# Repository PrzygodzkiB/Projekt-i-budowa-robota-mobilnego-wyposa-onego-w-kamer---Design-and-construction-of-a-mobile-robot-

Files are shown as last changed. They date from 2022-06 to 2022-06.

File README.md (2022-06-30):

# Design and construction of a mobile robot 
## English
This engineering thesis is written in Polish. However, if someone wants to see the code for ESP 32 CAM microcontrollers for transmitting the image from the camera and ESP 32 for controlling the control via wifi, you are welcome. 

The work presents the construction process and implementation of a mobile robot software
equipped with a camera. Its assumption is to construct a remotely controlled unit enabling
smooth image transmission. The scope of work is also related to the commissioning and testing
of the constructed structure.

The completed vehicle was designed to work well at home. It was with this in mind that
the engines and the platform were selected. During the design stage, it was decided to use
two microcontrollers, due to the limitations of one of them and the desire to liquefy the
camera image. The method of selecting a driver for motors, sonars, power source and voltage
stabilizer has also been described. When designing the electronic part, care was taken to ensure
the appropriate temperature of the system and safety in the event of short circuits. Schematic
diagrams and block diagrams of electrical connections in the system are also presented. There
is also a description of two hand-designed PCBs.

As part of the work, the robot successfully communicated with the user via wi-fi. A website
was also written to serve as a driving control panel. It contains the image from the robot’s
camera as well as the results of distance and voltage measurements. UART’s communications
were also used to pass commands between the microcontrollers.

In order to drive the robot in a straight line, three methods of regulation were compared.
They were made on the basis of PI regulators, which synchronized the work of the engines or
did not do it. There are also written anti-collision functions while driving based on distance
measurements made with the use of sonars.
## Polish

Praca przedstawia proces budowy oraz implementację oprogramowania robota mobilnego
wyposażonego w kamerę. Jej założeniem jest skonstruowanie zdalnie sterowanej jednostki
umożliwiającej płynne przekazywanie obrazu. Zakres pracy wiąże się również z uruchomieniem
i przetestowaniem wykonanej konstrukcji.

Analizując tematykę zagadnienia, dokonano zestawienia trzech robotów z kamerą. Do
tego celu wybrano konstrukcje o zróżnicowanej budowie oraz przeznaczeniu. Z ich opisów
zaczerpnięto zastosowania później wykorzystane we własnym robocie.

Wykonany pojazd został zaprojektowany tak, aby sprawdzał się w warunkach domowych.
Pod tym kątem dokonano wyboru silników oraz platformy. W czasie projektowania zdecydowano
się na użycie dwóch mikrokontrolerów, z powodów ograniczeń jednego z nich oraz
z chęci upłynnienia obrazu kamery. Dokonano również opisu sposobu doboru sterownika
silników, sonarów, źródła zasilania oraz stabilizatora napięcia. Projektując część elektroniczną,
zadbano o odpowiednią temperaturę układu oraz o bezpieczeństwo w przypadku wystąpienia
zwarć. Przedstawiono też schematy ideowe oraz blokowe połączeń elektrycznych w układzie.
Umieszczono również opis dwóch własnoręcznie zaprojektowanych płytek PCB.

W ramach pracy dokonano udanej komunikacji robota z użytkownikiem za pomocą wi-fi.
Napisano również stronę internetową służącą jako panel kontroli jazdy. Witryna wyświetla obraz
z kamery robota oraz wyniki pomiarów odległości i napięcia. Zastosowano również komunikacje
UART w celu przekazywania poleceń między mikrokontrolerami.

Aby zrealizować jazdę robota po linii prostej, dokonano porównania trzech sposobów
regulacji. Były one zrealizowane na postawie regulatorów PI, które synchronizowały prace
silników lub tego nie robiły. Napisano również funkcje zabezpieczające przed kolizją w czasie
jazdy na podstawie pomiarów odległości wykonywanych za pomocą sonarów.

W czasie testów dokonano oceny otrzymywanego obrazu. Okazał on się płynny i wyraźny
na tyle, by zidentyfikować co, znajduje się w otoczeniu robota. Za pomocą wyników testu
jazdy po linii prostej wykonano zestawienie osiągnięć różnych sposobów sterowania. Udało
się dzięki temu wytypować najlepszy z nich. Dokonano również sprawdzenia bezkolizyjności
robota. Zastosowane sonary okazały się wystarczające, jednak znaleziono też wady użytego
zastosowania. Można uznać, że całościowy projekt sprawdził się w swoim przeznaczeniu.

## Pictures

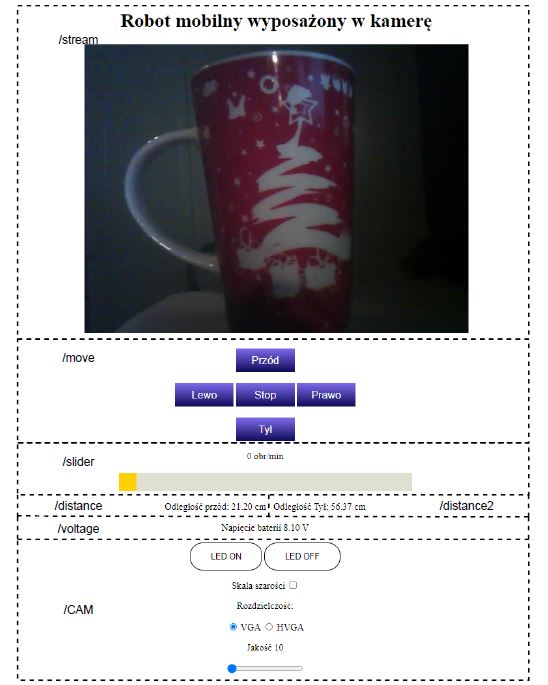
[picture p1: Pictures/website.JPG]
website to communicate with robot


Website to communicate with robot

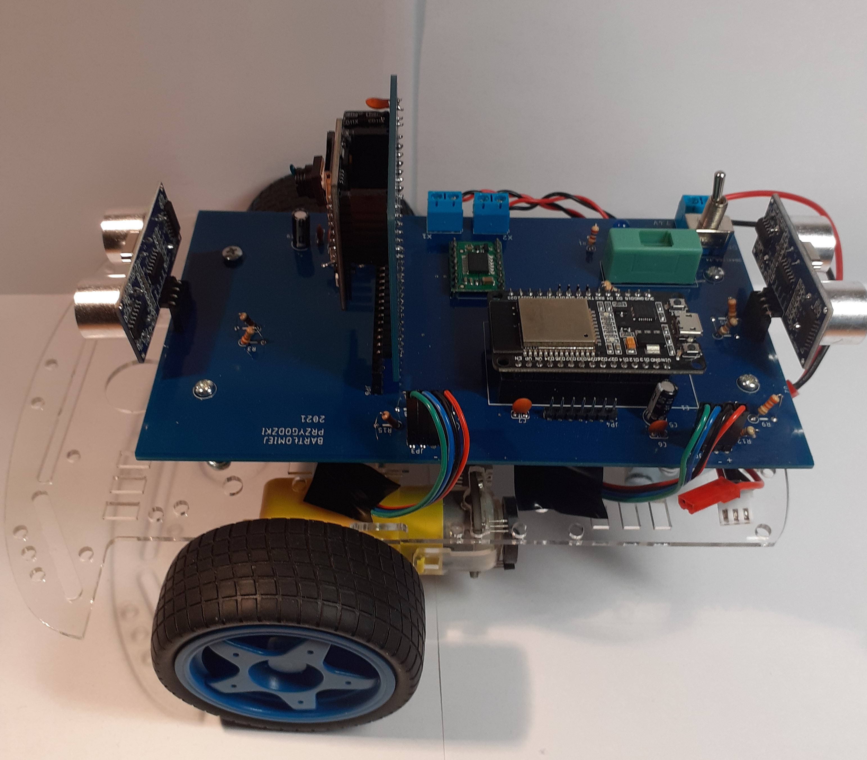
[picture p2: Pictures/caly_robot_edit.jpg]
Robot


Robot

Feel free to use

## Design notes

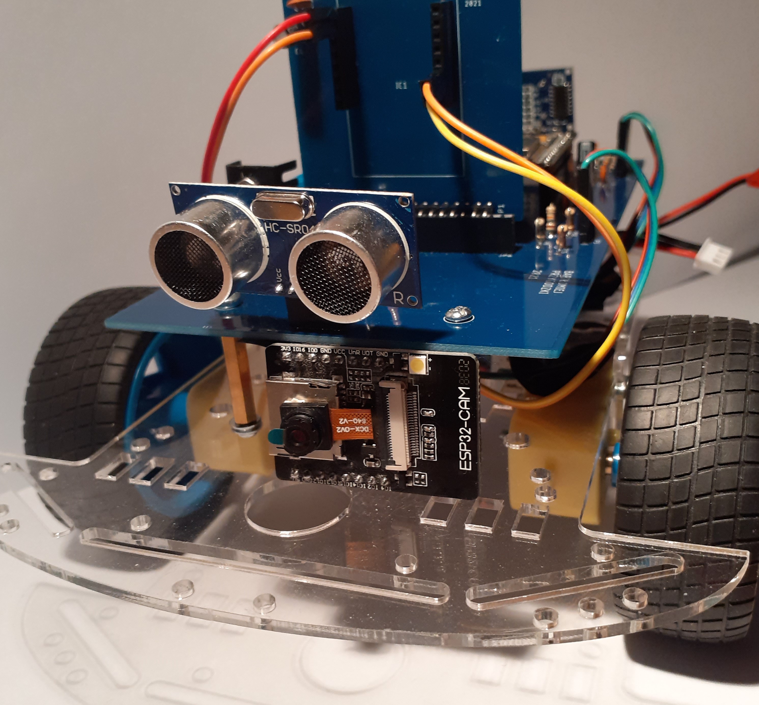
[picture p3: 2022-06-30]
Pictures/robot_inne_ustawienie_kamery.jpg

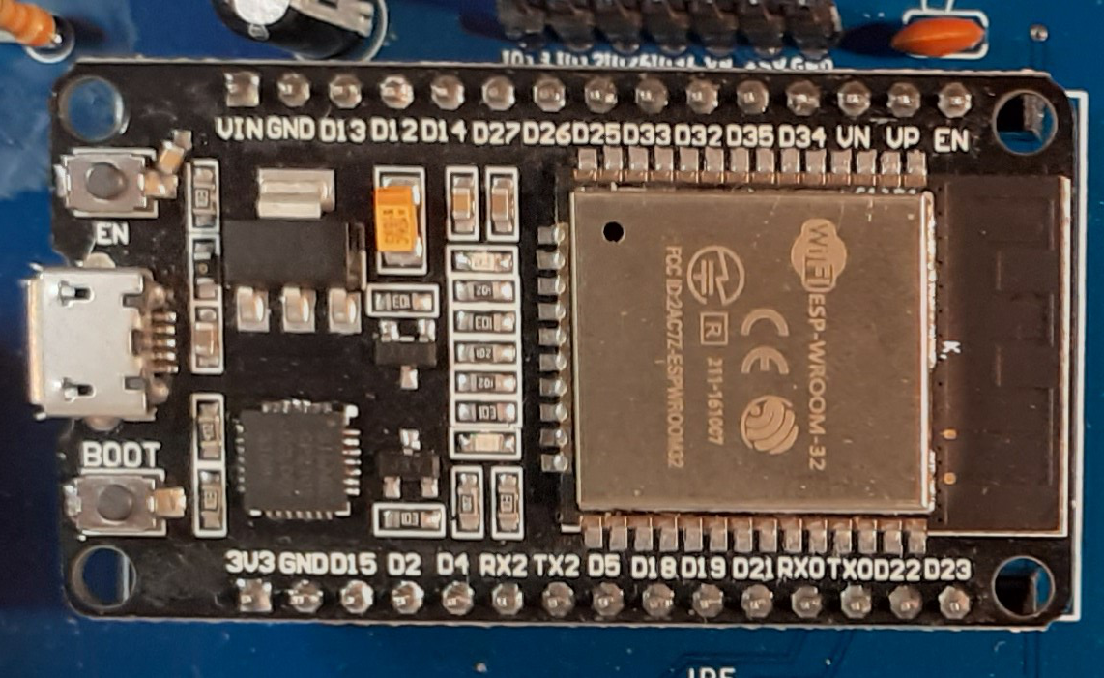
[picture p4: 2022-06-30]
Pictures/devkit.jpg

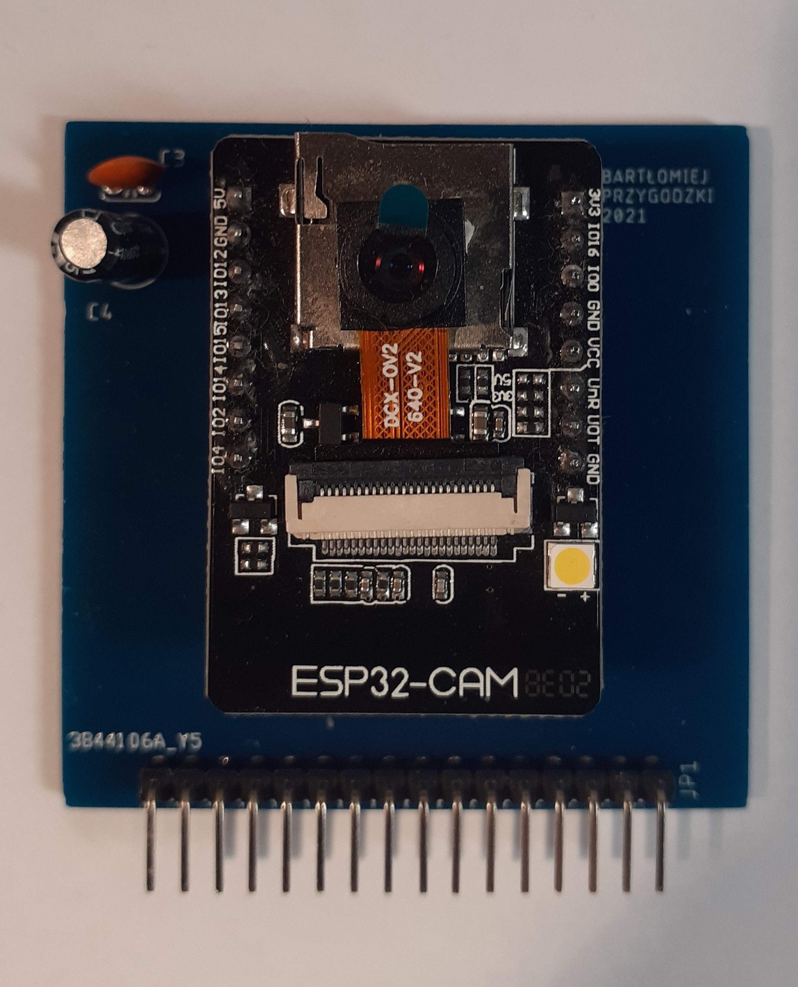
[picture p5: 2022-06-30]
Pictures/Płytka_z_ESP32CAM_edit.jpg

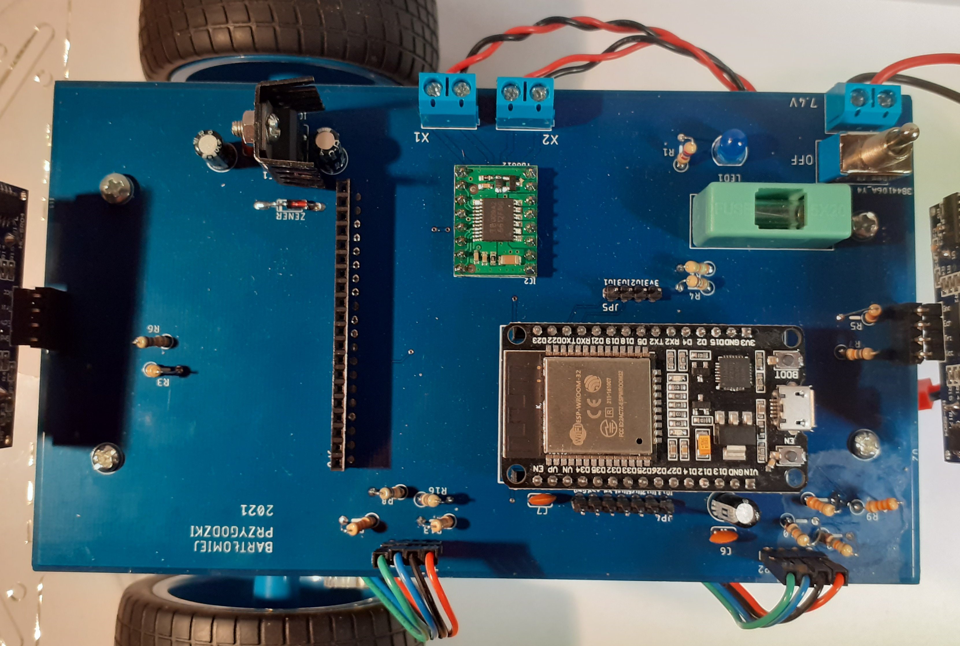
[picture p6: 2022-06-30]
Pictures/płytka_główna_edit.jpg

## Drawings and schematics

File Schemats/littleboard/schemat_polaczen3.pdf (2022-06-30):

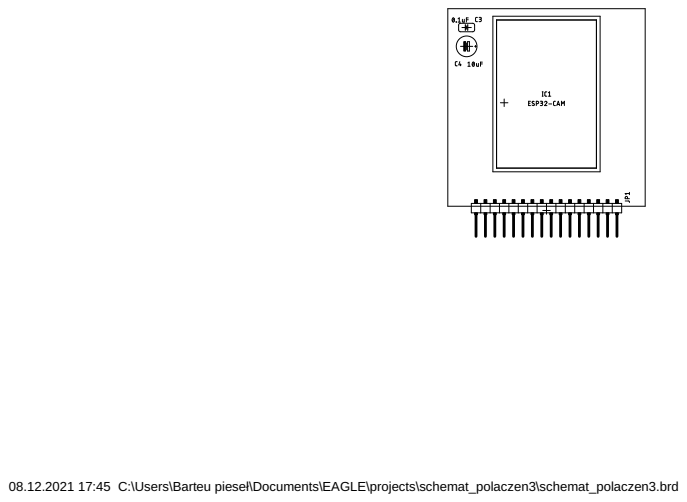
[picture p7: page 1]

08.12.2021 17:45 C:\Users\Barteu pieseł\Documents\EAGLE\projects\schemat_polaczen3\schemat_polaczen3.brd

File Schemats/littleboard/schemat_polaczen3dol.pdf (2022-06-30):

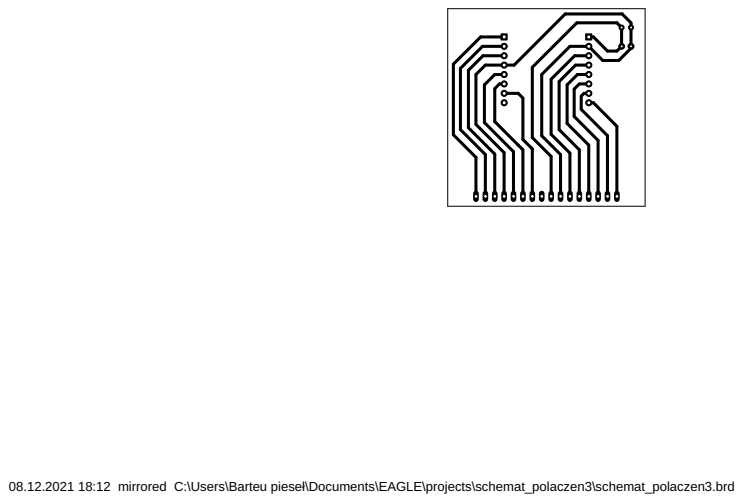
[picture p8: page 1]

08.12.2021 18:12 mirrored C:\Users\Barteu pieseł\Documents\EAGLE\projects\schemat_polaczen3\schemat_polaczen3.brd

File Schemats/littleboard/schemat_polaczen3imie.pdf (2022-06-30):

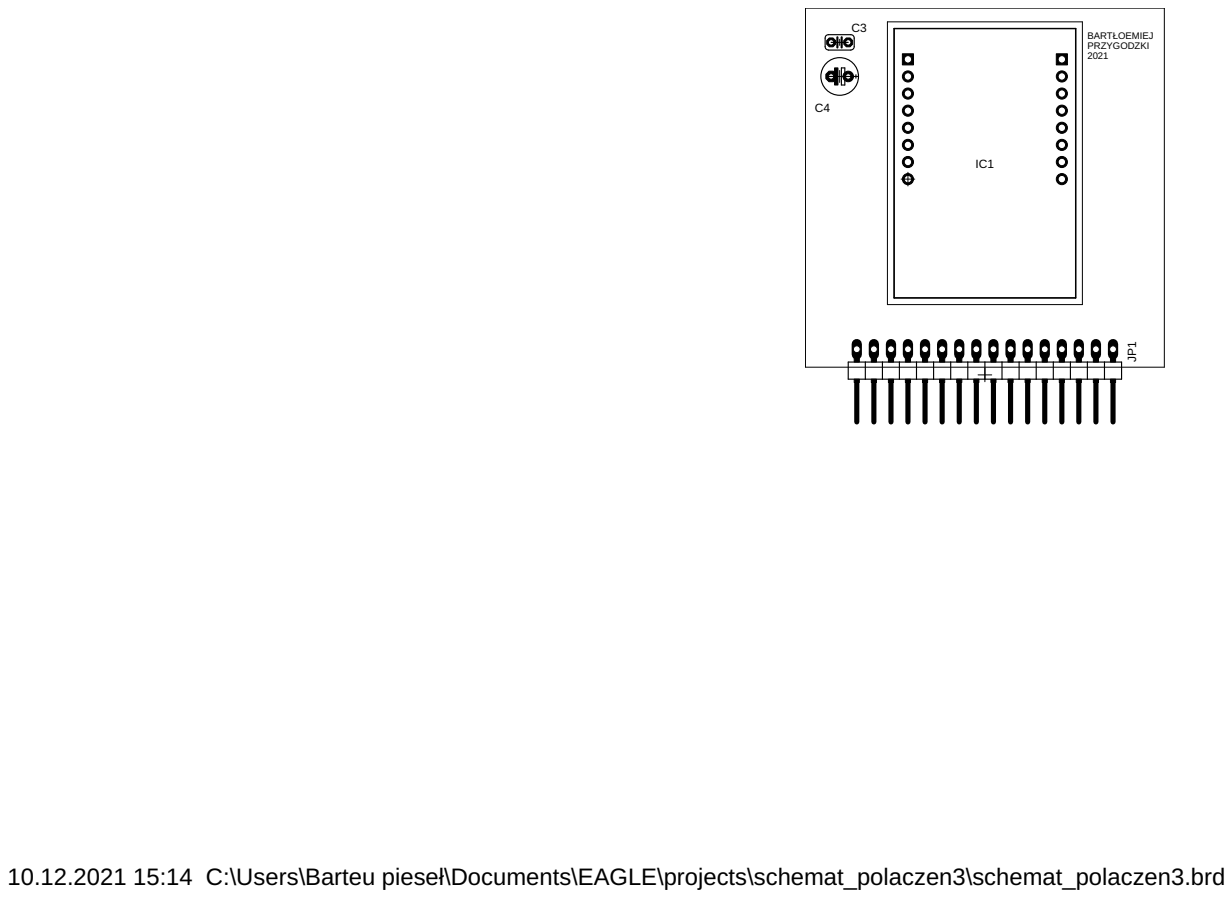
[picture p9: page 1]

10.12.2021 15:14 C:\Users\Barteu pieseł\Documents\EAGLE\projects\schemat_polaczen3\schemat_polaczen3.brd

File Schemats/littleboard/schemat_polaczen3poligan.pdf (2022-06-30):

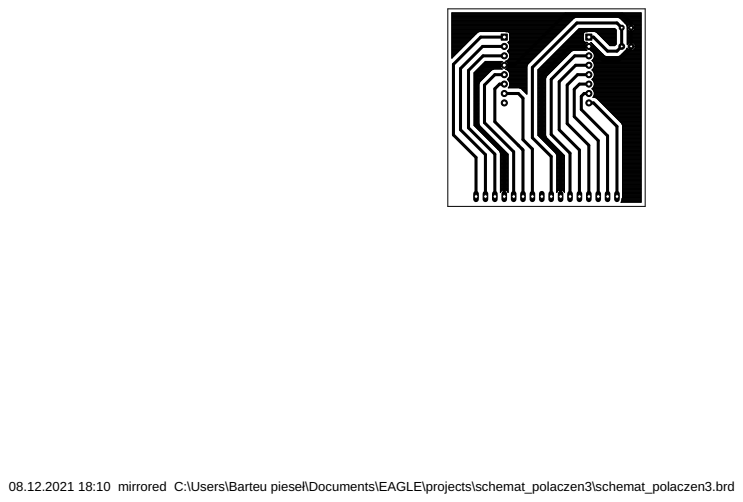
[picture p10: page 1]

08.12.2021 18:10 mirrored C:\Users\Barteu pieseł\Documents\EAGLE\projects\schemat_polaczen3\schemat_polaczen3.brd

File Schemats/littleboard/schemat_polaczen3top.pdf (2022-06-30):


08.12.2021 17:45 C:\Users\Barteu pieseł\Documents\EAGLE\projects\schemat_polaczen3\schemat_polaczen3.brd

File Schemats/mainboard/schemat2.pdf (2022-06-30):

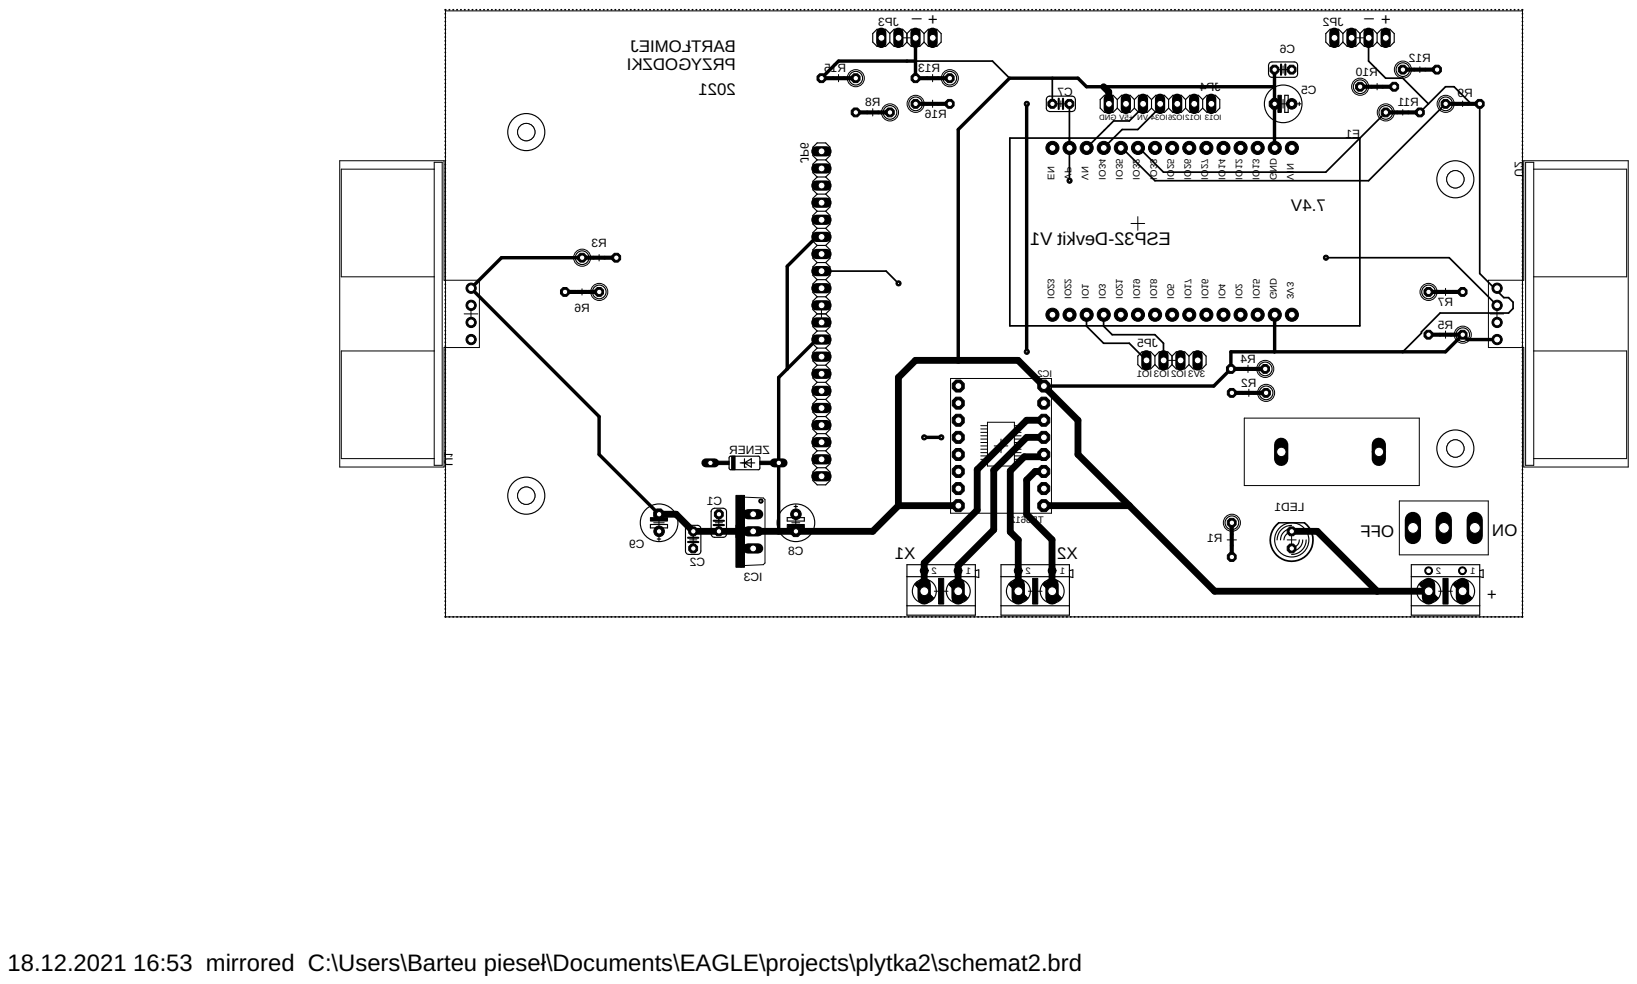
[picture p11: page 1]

18.12.2021 16:53 mirrored C:\Users\Barteu pieseł\Documents\EAGLE\projects\plytka2\schemat2.brd

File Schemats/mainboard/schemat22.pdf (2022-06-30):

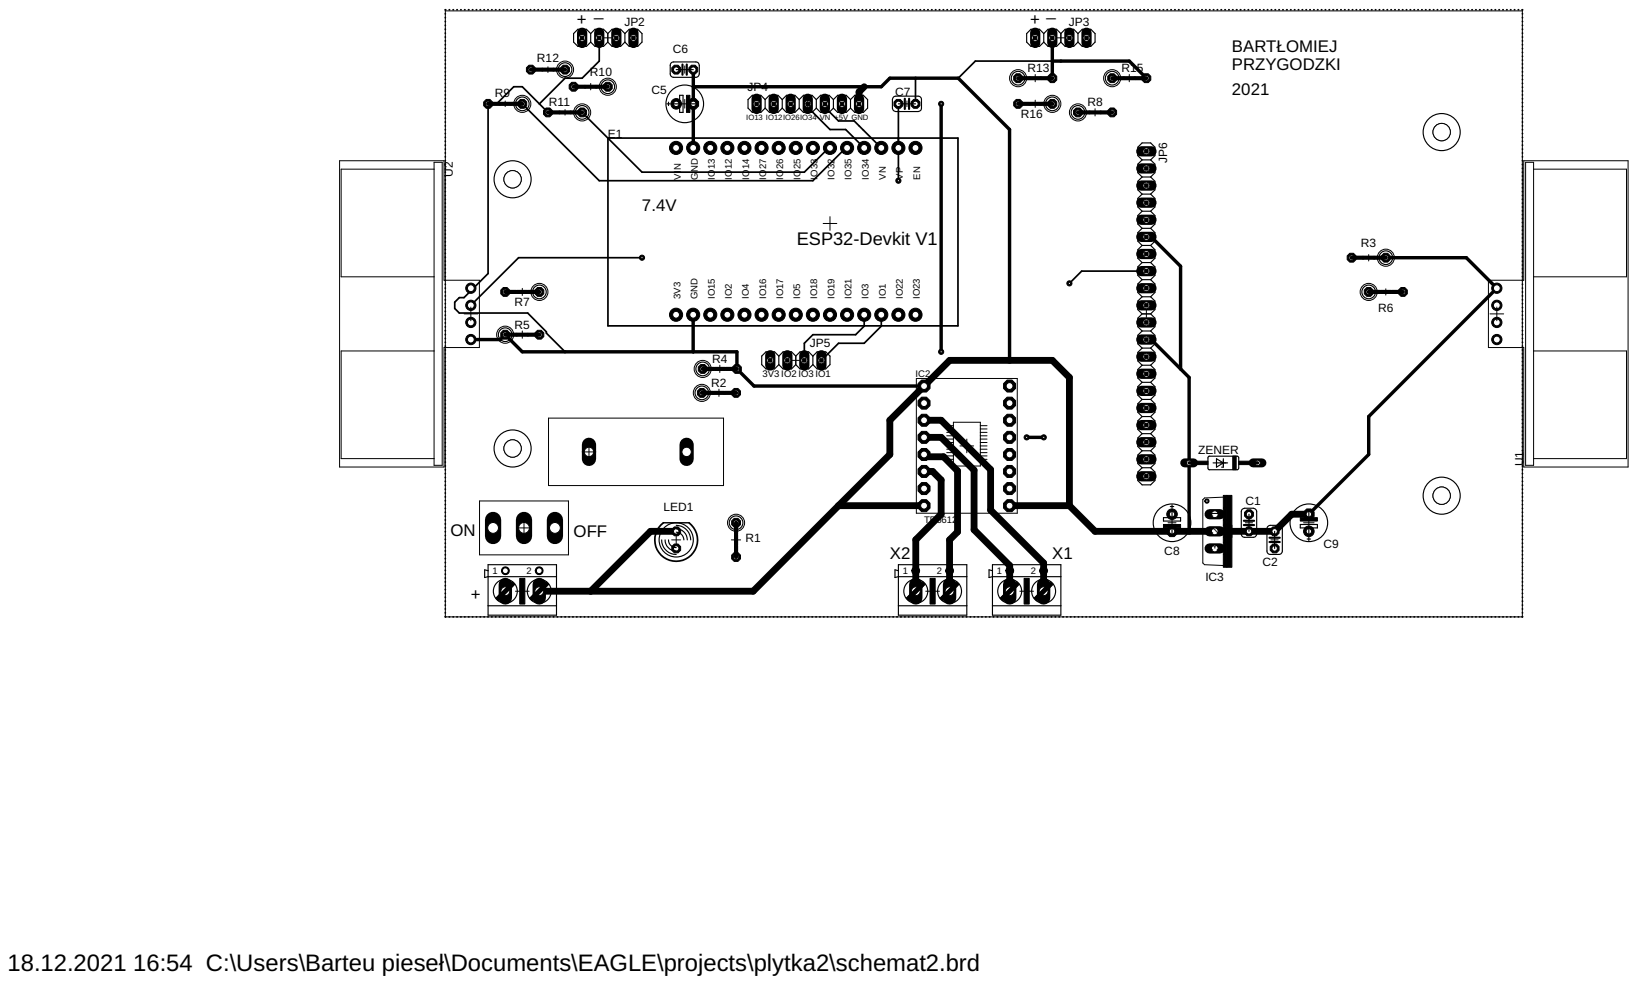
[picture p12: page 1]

18.12.2021 16:54 C:\Users\Barteu pieseł\Documents\EAGLE\projects\plytka2\schemat2.brd

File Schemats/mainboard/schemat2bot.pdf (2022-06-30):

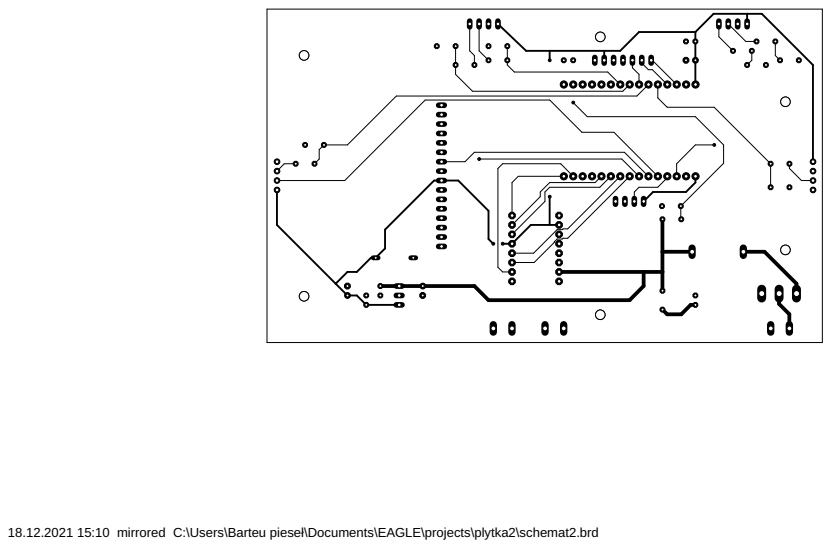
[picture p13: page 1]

18.12.2021 15:10 mirrored C:\Users\Barteu pieseł\Documents\EAGLE\projects\plytka2\schemat2.brd

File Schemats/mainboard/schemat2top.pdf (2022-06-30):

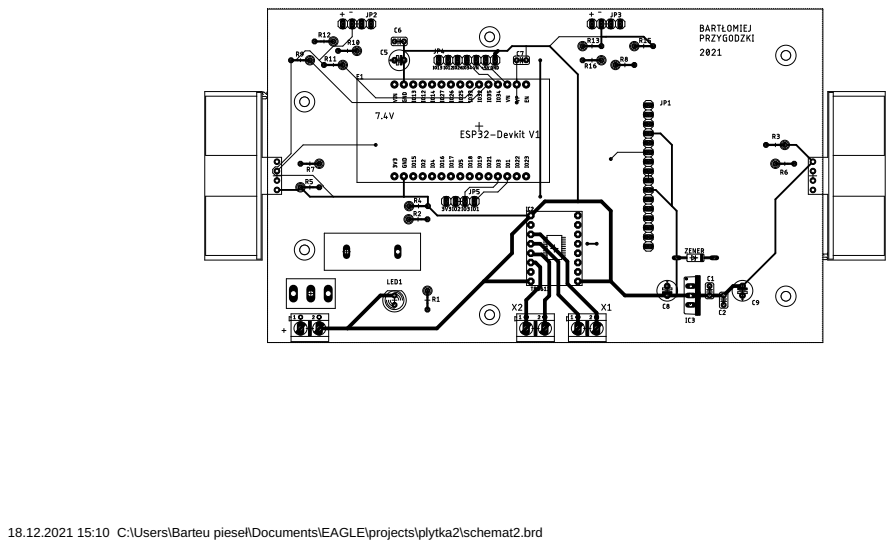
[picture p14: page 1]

18.12.2021 15:10 C:\Users\Barteu pieseł\Documents\EAGLE\projects\plytka2\schemat2.brd

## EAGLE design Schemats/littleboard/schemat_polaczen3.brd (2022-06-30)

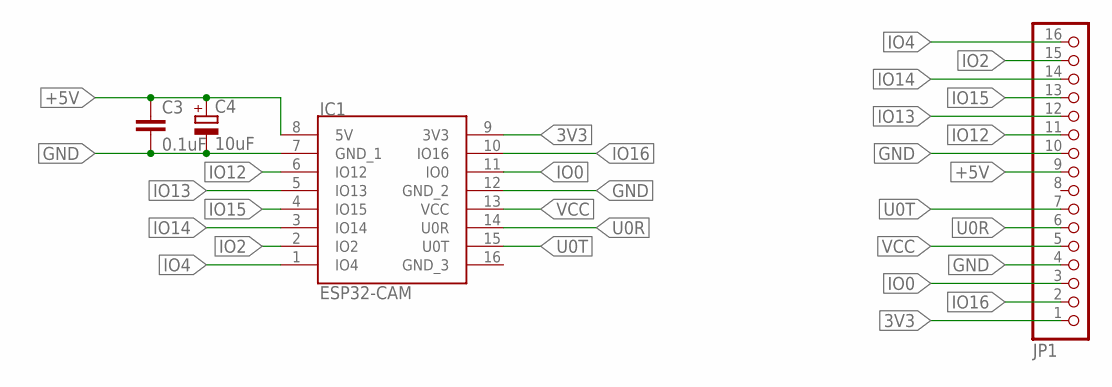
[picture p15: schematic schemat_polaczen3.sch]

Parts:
C3: 0.1uF; C025-024X044
C4: 10uF; E2,5-6E
IC1: ESP32-CAM; ESP32CAM
JP1: PINHD-1X16/90; 1X16/90

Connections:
3V3: IC1.9 (3V3), JP1.1
+5V: C3.1, C4.+, IC1.8 (5V), JP1.9
GND: C3.2, C4.-, IC1.7 (GND_1), IC1.12 (GND_2), JP1.4, JP1.10
IO0: IC1.11 (IO0), JP1.3
IO2: IC1.2 (IO2), JP1.15
IO4: IC1.1 (IO4), JP1.16
IO12: IC1.6 (IO12), JP1.11
IO13: IC1.5 (IO13), JP1.12
IO14: IC1.3 (IO14), JP1.14
IO15: IC1.4 (IO15), JP1.13
IO16: IC1.10 (IO16), JP1.2
U0R: IC1.14 (U0R), JP1.6
U0T: IC1.15 (U0T), JP1.7
VCC: IC1.13 (VCC), JP1.5

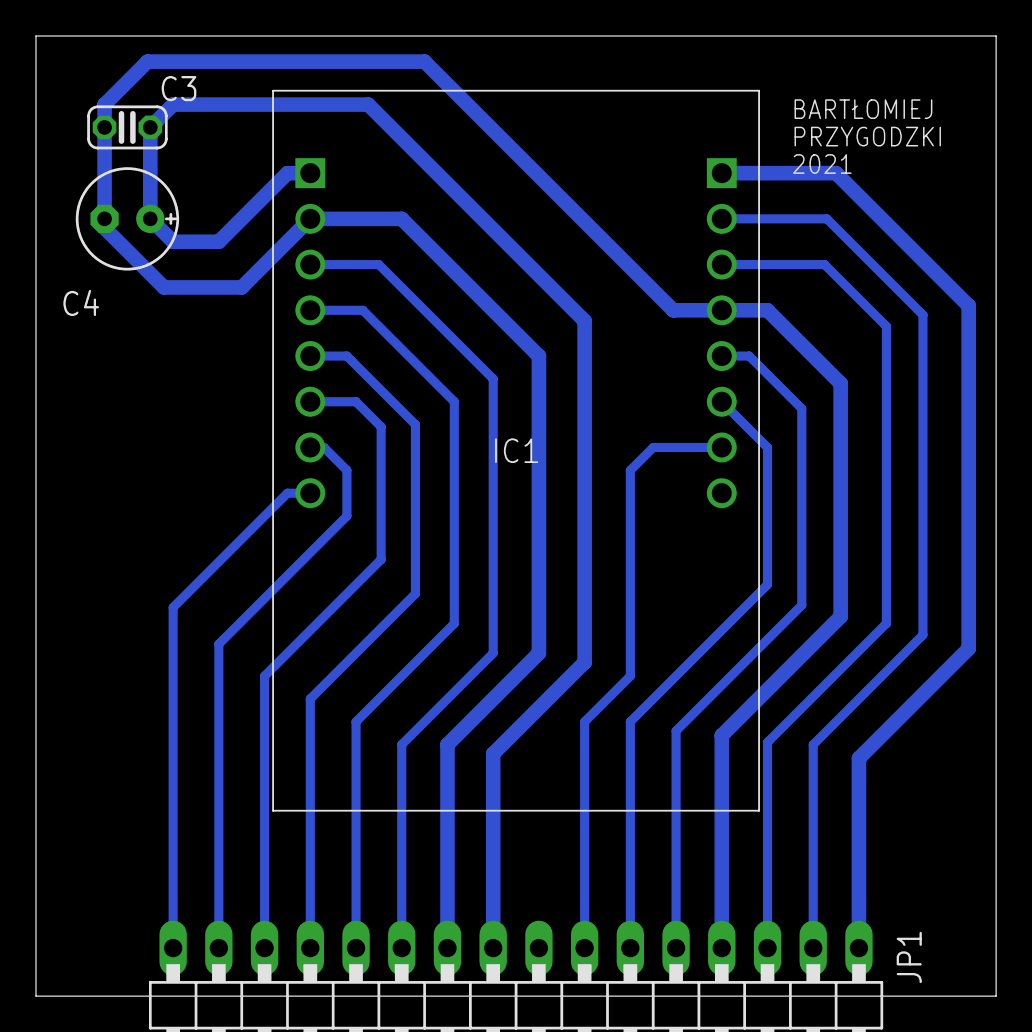
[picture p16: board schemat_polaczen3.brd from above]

Board: 2 copper layers, 53.3 x 53.3 mm, 4 parts (0 on the bottom side), 14 nets.

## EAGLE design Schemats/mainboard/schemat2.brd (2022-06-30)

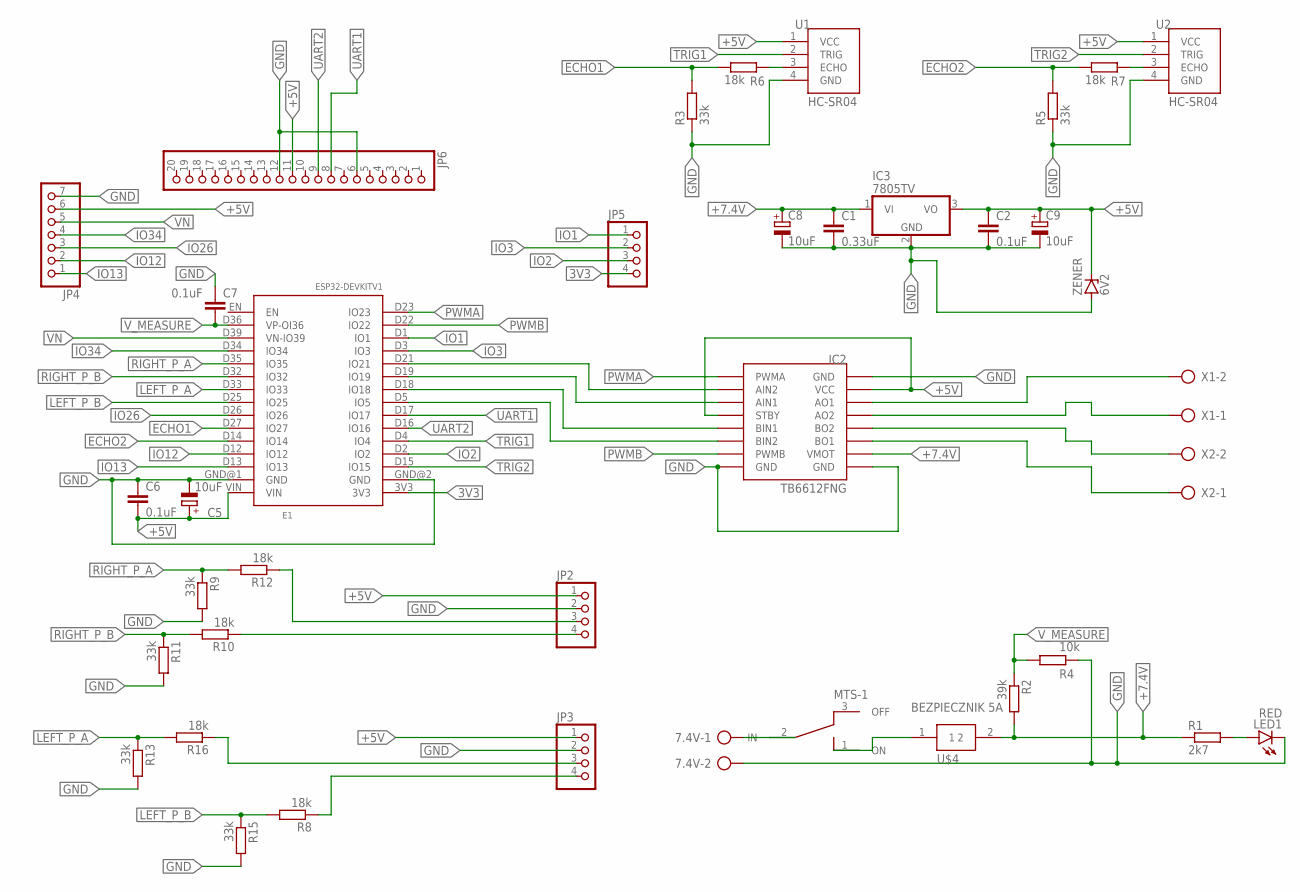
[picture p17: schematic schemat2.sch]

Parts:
7.4V: AK500/2
C1: 0.33uF; C025-024X044
C2, C6, C7: 0.1uF; C025-024X044
C5, C8, C9: 10uF; E2,5-6E
E1: ESP32DEVKITV1; ESP32-DEVKITV1
IC2: MODUL_POLOLU
IC3: 7805TV; TO220V
JP2, JP3, JP5: PINHD-1X4; 1X04
JP4: PINHD-1X7; 1X07
JP6: PINHD-1X20; 1X20
LED1: RED; LED5MM
R1: 2k7; 0207/5V
R2: 39k; 0207/5V
R3, R5, R9, R11, R13, R15: 33k; 0207/5V
R4: 10k; 0207/5V
R6, R7, R8, R10, R12, R16: 18k; 0207/5V
U1, U2: HC-SR04; XCVR_HC-SR04
U$1: MTS-1; SWITCH_TOGGLE
U$4: BEZPIECZNIK 5A; BEZPIECZNIK_GNIAZDO
X1, X2: AK500/2
ZENER: 6V2; DO35Z10

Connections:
3V3: E1.3V3, JP5.4
+5V: C2.1, C5.+, C6.2, C9.+, E1.VIN, IC2.STBY, IC2.VCC, IC3.3 (VO), JP2.1, JP3.1, JP4.6, JP6.11, U1.1 (VCC), U2.1 (VCC), ZENER.C
+7.4V: C1.1, C8.+, IC2.VMOT, IC3.1 (VI), R1.1, R2.2, U$4.2
A: JP3.3, R16.1
A1: JP2.3, R12.1
B: JP3.4, R8.1
B1: JP2.4, R10.1
ECHO1: E1.D27 (IO27), R3.2, R6.1
ECHO2: E1.D14 (IO14), R5.2, R7.1
GND: 7.4V.2, C1.2, C2.2, C5.-, C6.1, C7.1, C8.-, C9.-, E1.GND@1 (GND), E1.GND@2 (GND), IC2.GND1 (GND), IC2.GND2 (GND), IC2.GND3 (GND), IC3.2 (GND), JP2.2, JP3.2, JP4.7, JP6.6, JP6.12, LED1.K (C), R3.1, R4.2, R5.1, R9.2, R11.2, R13.2, R15.2, U1.4 (GND), U2.4 (GND), ZENER.A
IO1: E1.D1 (IO1), JP5.1
IO2: E1.D2 (IO2), JP5.3
IO3: E1.D3 (IO3), JP5.2
IO12: E1.D12 (IO12), JP4.2
IO13: E1.D13 (IO13), JP4.1
IO26: E1.D26 (IO26), JP4.3
IO34: E1.D34 (IO34), JP4.4
LEFT_P_A: E1.D33 (IO33), R13.1, R16.2
LEFT_P_B: E1.D25 (IO25), R8.2, R15.1
L_MOT+: IC2.BO2, X2.2
L_MOT-: IC2.BO1, X2.1
unnamed: LED1.A, R1.2
unnamed: R6.2, U1.3 (ECHO)
unnamed: R7.2, U2.3 (ECHO)
unnamed: 7.4V.1, U$1.2 (IN)
unnamed: E1.D5 (IO5), IC2.BIN2
unnamed: E1.D18 (IO18), IC2.BIN1
unnamed: E1.D21 (IO21), IC2.AIN2
unnamed: E1.D19 (IO19), IC2.AIN1
unnamed: U$1.1 (ON), U$4.1
PWMA: E1.D23 (IO23), IC2.PWMA
PWMB: E1.D22 (IO22), IC2.PWMB
RIGHT_P_A: E1.D35 (IO35), R9.1, R12.2
RIGHT_P_B: E1.D32 (IO32), R10.2, R11.1
R_MOT+: IC2.AO1, X1.2
R_MOT-: IC2.A02 (AO2), X1.1
TRIG1: E1.D4 (IO4), U1.2 (TRIG)
TRIG2: E1.D15 (IO15), U2.2 (TRIG)
UART1: E1.D17 (IO17), JP6.8
UART2: E1.D16 (IO16), JP6.9
VN: E1.D39 (VN-IO39), JP4.5
V_MEASURE: C7.2, E1.D36 (VP-OI36), R2.1, R4.1

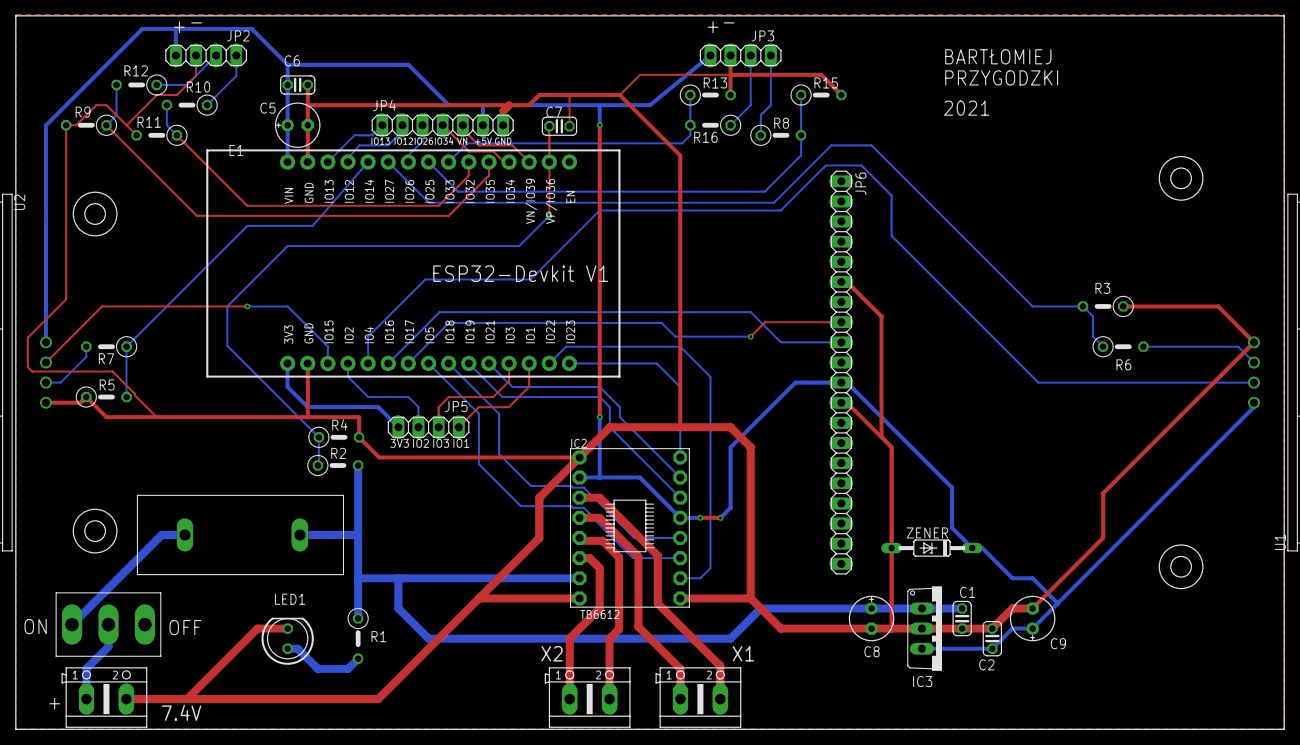
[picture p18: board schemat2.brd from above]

Board: 2 copper layers, 160.0 x 90.0 mm, 39 parts (0 on the bottom side), 42 nets.

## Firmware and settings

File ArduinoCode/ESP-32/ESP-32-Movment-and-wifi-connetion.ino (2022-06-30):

#include <WiFi.h>
#include <AsyncTCP.h>
#include <ESPAsyncWebServer.h>
#include "soc/soc.h"
#include "soc/rtc_cntl_reg.h"
#include <HardwareSerial.h>


const char *ssid = "Orange_Swiatlowod_095A";
const char *password = "WWZYKLF6PR4V";//dane sieci

HardwareSerial mySerial(1);


IPAddress local_IP(192, 168, 1, 29);
//aby zobaczyc sterowania
//http://192.168.1.31
//http://192.168.1.29
//http://192.168.1.29/distance
//http://192.168.1.29/slider
//skozystaj z linkow
IPAddress gateway(192, 168, 1, 2);
IPAddress subnet(255, 255, 0, 0);
IPAddress primaryDNS(8, 8, 8, 8);
IPAddress secondaryDNS(8, 8, 4, 4);

//sterownik silnika
#define PWMA 23
#define PWMB 22
#define BIN2 5//lewy silnik - B
#define BIN1 18
#define AIN2 21//prawy silnik - A
#define AIN1 19
#define chanell 8//kanał PWN do sterownika
#define PWM_Freq  4000
#define PWM_Res 8
#define MAX_PWM 230//max do 7.5 V i ma byc 
//przy 6 V to 160obr  165 PWM
//przy 3 V to 60obr  83 PWM

//sonar
#define trigPin  4
#define echoPin  27
#define SOUND_SPEED_HALF 0.017//polowa prekosci swiatla
//pomiar v
#define trigPin2  15
#define echoPin2  14
//pomiar napiecia
#define v_baterry  36

//enkoder
#define ENC2A 35
#define ENCA 33
//UART
#define RXD2 16
#define TXD2 17

long prevT = 0;
int posPrev = 0;

int pos_i = 0;
float velocity = 0.0;
float velocity2 = 0.0;
long prevT_i = 0;
long prevT_iP = 0;
float v2Prev = 0.0;

float v1Prev = 0.0;
float v_in = 0.0;
float v_in1 = 0.0;
float v_in2 = 0.0;
float v_in3 = 0.0;
int i =0;
bool left_encoder=false;
long deltaT =0;
bool right_encoder=false;
long deltaTP =0;
int incrementP= 1;
int incrementL= 1;
long lastMillis =0;
float tab[]={0,0,0,0,0,0,0,0,0,0};
int num=0;
int a=0;
int setpoint = 0;
int setpoint2 = 0;
float deltaTC =0.0;
volatile bool interruptpi=false;
volatile bool interruptdist=false;
volatile bool interruptpomiar=false;
String Front="";
String Back="";
float v1Filt = 0.0;
float v1PrevF = 0.0;

float v2Filt = 0.0;
float v2PrevF = 0.0;



hw_timer_t * timer = NULL;
hw_timer_t * timer1 = NULL;
hw_timer_t * timer2 = NULL;
portMUX_TYPE timerMux = portMUX_INITIALIZER_UNLOCKED;

float prevT_iC =0.0;
/* zwykły PID
float  kp=10.0;
float ki=24.0;
float kp2=10.0;
float ki2=24.0;
*/
 



/*// z samą synchronizacją kół
float kp=10.0;
float ki=24.0;
float kp2=32.0;
float ki2=200.0; 

*/


float kp=10.0;
float ki=24.0;

float kp2=10.0;
float ki2=24.0; 

float kp3=32.0;
float ki3=200.0; 
//ostatni regulator


float e=0.0;
float u=0.0;
float calka=0.0;
float dr=0.0;
float ep=0.0;

float e2=0.0;
float u2=0.0;
float calka2=0.0;
float dr2=0.0;
float ep2=0.0;
float pr1=0.0;

float e3=0.0;
float calka3=0.0;


String button = "stop";//kierunek jazdy
float Distance_Cm=0.0;
float Distance_Cm2=0.0;
float lastDistance_Cm=0.0;
float lastDistance_Cm2=0.0;
bool error_front = 0;//wykrycie kolizji
bool error_back = 0;//wykrycie kolizji
int colision_distance = 20;//dopuszczalny dystans
String pwmSliderValue = "0";

AsyncWebServer server(80);
void EncoderL();
void IRAM_ATTR check_EncoderL();
void IRAM_ATTR check_EncoderP();
void EncoderP();

void IRAM_ATTR onTimer() {
  portENTER_CRITICAL_ISR(&timerMux);
  interruptpi=true;
  portEXIT_CRITICAL_ISR(&timerMux);
 
}
void IRAM_ATTR onTimer1() {
  portENTER_CRITICAL_ISR(&timerMux);
  interruptpomiar=true;
  portEXIT_CRITICAL_ISR(&timerMux);
 
}
void IRAM_ATTR onTimer2() {
  portENTER_CRITICAL_ISR(&timerMux);
  interruptdist=true;
  portEXIT_CRITICAL_ISR(&timerMux);
 
}
void move(String direction)
{ // wykonanie polecenia z przegladarki
  //z uwzglednieniem kolizji
  
  if (direction == "forward" && !colision_detect()) {
   // Serial.println("Forward");
   setpoint=abs(setpoint);
    digitalWrite(AIN1, HIGH);
    digitalWrite(AIN2, LOW);
    digitalWrite(BIN1, HIGH);
    digitalWrite(BIN2, LOW);
    setpoint2=1;
  }
  if (direction == "left") {
   //Serial.println("Left");
    digitalWrite(AIN1, HIGH);
    digitalWrite(AIN2, LOW);
    digitalWrite(BIN1, LOW);
    digitalWrite(BIN2, HIGH);
    //setpoint=-abs(setpoint);
    //setpoint2=-1;
  }
  if (direction == "right") {
   // Serial.println("Right");
//setpoint=abs(setpoint);
    digitalWrite(AIN1, LOW);
    digitalWrite(AIN2, HIGH);
    digitalWrite(BIN1, HIGH);
    digitalWrite(BIN2, LOW);
    //setpoint2=-1;
  }
  if (direction == "backward"&& !colision_detect_back()) {
    //Serial.println("Backward");
    digitalWrite(AIN1, LOW);
    digitalWrite(AIN2, HIGH);
    digitalWrite(BIN1, LOW);
    digitalWrite(BIN2, HIGH);
    //setpoint=-abs(setpoint);
    //setpoint2=1;
  }
  if (direction == "stop") {
   // Serial.println("Stop");
    digitalWrite(AIN1, LOW);
    digitalWrite(AIN2, LOW);
    digitalWrite(BIN1, LOW);
    digitalWrite(BIN2, LOW);
    e=0.0;
    u=0.0;
    calka=0.0;
    e2=0.0;
    u2=0.0;
    calka2=0.0;
    dr=0.0;
    ep=0.0;

    e3=0.0;
    
    calka3=0.0;
  }
}

bool colision_detect()
{
  //detekcja kolizji oraz zatrzymanie robota
  if (Distance_Cm > colision_distance && button == "forward" && lastDistance_Cm <= colision_distance)
  {
    lastDistance_Cm = Distance_Cm;
    error_front = 0;
    button = "forward";
    move("forward");
    return 0;

  }
  else if (Distance_Cm <= colision_distance && button == "forward")
  {
    lastDistance_Cm = Distance_Cm;
    error_front = 1;
    button = "stop";
    move("stop");
    return 1;
  }
  else
  {
    lastDistance_Cm = Distance_Cm;
    error_front = 0;
    return 0;
  }
 
}
bool colision_detect_back()
{
  //detekcja kolizji oraz zatrzymanie robota
  if (Distance_Cm2 > colision_distance && button == "backward" && lastDistance_Cm2 <= colision_distance)
  {//juz nie ma kolizji
    lastDistance_Cm2 = Distance_Cm2;
    error_back = 0;
    button = "backward";
    move("backward");
    return 0;

  }
  else if (Distance_Cm2 <= colision_distance && button == "backward")
  {
    lastDistance_Cm2 = Distance_Cm2;
    error_back = 1;
    button = "stop";
    move("stop");
    return 1;
  }
  else
  {
    lastDistance_Cm2 = Distance_Cm2;
    error_back = 0;
    return 0;
  }
 
}
String v_measure()
{
 // v_in = (analogRead(v_baterry)/4095.0)*3.3) * 2.8;//28000/100000=2.8 z dzielnika napiecia
  v_in = ((analogRead(v_baterry)/4095.0)*3.3+0.19)*4.9;
  v_in3=v_in2;
  v_in2=v_in1;
  v_in1=v_in;
  v_in=(v_in1+v_in2+v_in3)/3.0;
  
   return String(v_in, 2);
}
void Front_sensor()
{
  //obsluga HC-SR04
  digitalWrite(trigPin, LOW);
  delayMicroseconds(2);
  digitalWrite(trigPin, HIGH);
  delayMicroseconds(10);
  digitalWrite(trigPin, LOW);
  // Sposob proponowany przez producenta
  Distance_Cm = pulseIn(echoPin, HIGH) * SOUND_SPEED_HALF;
  
  //Serial.print("Distance (cm): ");
  //Serial.println(Distance_Cm);
  
  colision_detect();
  
  Front=String(Distance_Cm, 2);
}
void Back_sensor()
{
  //obsluga HC-SR04
  digitalWrite(trigPin2, LOW);
  delayMicroseconds(2);
  digitalWrite(trigPin2, HIGH);
  delayMicroseconds(10);
  digitalWrite(trigPin2, LOW);
  // Sposob proponowany przez producenta
  Distance_Cm2 = pulseIn(echoPin2, HIGH) * SOUND_SPEED_HALF;
  
 // Serial.print("Distance (cm): ");
 // Serial.println(Distance_Cm2);
  
  colision_detect_back();
  
  Back=String(Distance_Cm2, 2);
}

//czysty string
const char index_html[] PROGMEM = R"rawliteral(
<html>
  <head>
    <title>Praca inżynierska</title>
    <meta charset="UTF-8">
    <style>
      body {text-align: center;}
      table { margin-left: auto; margin-right: auto; }
.button {
    display: inline-block;
    text-align: center;
    vertical-align: middle;
    height:40px;
    width:100px;
     cursor: pointer;
    border: 0px solid #ffffff;
    border-radius: 0px;
    background: #7e6bed;
    background: -webkit-gradient(linear, left top, left bottom, from(#7e6bed), to(#0e0b57));
    background: -moz-linear-gradient(top, #7e6bed, #0e0b57);
    background: linear-gradient(to bottom, #7e6bed, #0e0b57);
    font: 18px arial;
    color: #ffffff;
   
}
.button:hover,
.button:focus {
    background: #9780ff;
    background: -webkit-gradient(linear, left top, left bottom, from(#9780ff), to(#110d68));
    background: -moz-linear-gradient(top, #9780ff, #110d68);
    background: linear-gradient(to bottom, #9780ff, #110d68);
    color: #ffffff;
}
.button:active {
    background: #4c408e;
    background: -webkit-gradient(linear, left top, left bottom, from(#4c408e), to(#0e0b57));
    background: -moz-linear-gradient(top, #4c408e, #0e0b57);
    background: linear-gradient(to bottom, #4c408e, #0e0b57);
}


      .Button2 {
  background:linear-gradient(to bottom, #ffffff 5%, #ffffff 100%);
  background-color:#ffffff;
  border-radius:22px;
  border:1px solid #000000;
  display:inline-block;
  cursor:pointer;
  color:#000000;
  font-family:Arial;
  font-size:14px;
  padding:15px 34px;
  text-decoration:none;
}
.Button2:hover {
  background:linear-gradient(to bottom, #ffffff 5%, #ffffff 100%);
  background-color:#ffffff;
}
.Button2:active {
  position:relative;
  top:1px;
}

      img {  width: auto ; height: auto ; }
      .slider1 {
        -webkit-appearance: none;
         width: 500;
         height: 30px;
         background: #e0e0d1;
        }
    .slider1::-webkit-slider-thumb {
        -webkit-appearance: none;
         width: 30px;
         height: 30px;
         cursor: pointer;
         background: #ffd100;
}
    </style>
  </head>
  <body>
    <h1>Robot mobilny wyposażony w kamerę</h1>
    
    <img src="http://192.168.1.27/stream" >
    <br>
    <br>
    <button class="button" onmousedown="toggleCheckbox('forward');" ontouchstart="toggleCheckbox('forward');" onmouseup="toggleCheckbox('stop');" ontouchend="toggleCheckbox('stop');">Przód</button>
      <br>
      <br>
    <button class="button" onmousedown="toggleCheckbox('left');" ontouchstart="toggleCheckbox('left');" onmouseup="toggleCheckbox('stop');" ontouchend="toggleCheckbox('stop');">Lewo</button>
     
    <button class="button" onmousedown="toggleCheckbox('stop');" ontouchstart="toggleCheckbox('stop');">Stop</button>

    <button class="button" onmousedown="toggleCheckbox('right');" ontouchstart="toggleCheckbox('right');" onmouseup="toggleCheckbox('stop');" ontouchend="toggleCheckbox('stop');">Prawo</button>
    <br>
    <br>
    <button class="button" onmousedown="toggleCheckbox('backward');" ontouchstart="toggleCheckbox('backward');" onmouseup="toggleCheckbox('stop');" ontouchend="toggleCheckbox('stop');">Tył</button> 
    
    <p><span id="textSliderValue">%SLIDERVALUE%</span> obr/min</p>
    <p><input type="range" onchange="updateSliderPWM(this)" id="pwmSlider" min="0" max="70" value="%SLIDERVALUE%" step="1" class="slider1"></p>
    
    <p>Odległość przód: <span id="distance">%DISTANCE%</span> cm &nbsp Odległość Tył: <span id="distance2">%DISTANCE2%</span> cm</p>
    <p>Napięcie baterii <span id="voltage">%VOLTAGE%</span> V</p>
    <button class="button2" onclick="on()">LED ON</button>
    <button class="button2" onclick="off()">LED OFF</button>
    
    <p><label>Skala szarości</label> 
<input type="checkbox" id="Check" onclick="check()"></p>
<p>Rozdzielczość:</p>

<label><input type="radio" name="res" onclick="check2()"checked> VGA</label>
<label><input type="radio" name="res" onclick="check3()"> HVGA</label>

<p>Jakość <span id="jakosc">%SLIDER%</span></p>
    <p><input type="range" onchange="updateSlider(this)" id="jakoscSlider" min="10" max="60" value="10" step="1" class="slider2"></p>
    
  </body>
   <script>

   function updateSlider(element) {
  var SliderValue = document.getElementById("jakoscSlider").value;
  document.getElementById("jakosc").innerHTML = SliderValue;
  console.log(SliderValue);
  var httpRequest = new XMLHttpRequest();
  httpRequest.open("GET", "/CAM?button=quality"+SliderValue, true);
  httpRequest.send();
}
   function check() {
  var Box = document.getElementById("Check");
  if (Box.checked == true){
    var xhr = new XMLHttpRequest();
     xhr.open("GET", "/CAM?button=Gray", true);
     xhr.send();
  } else {
    var xhr = new XMLHttpRequest();
     xhr.open("GET", "/CAM?button=No Effect", true);
     xhr.send();
  }
}
function check2() {
 
    var xhr = new XMLHttpRequest();
     xhr.open("GET", "/CAM?button=VGA", true);
     xhr.send();
  
}
function check3() {
   var xhr = new XMLHttpRequest();
     xhr.open("GET", "/CAM?button=HVGA", true);
     xhr.send();
  }

   function toggleCheckbox(x) {
     var xhr = new XMLHttpRequest();
     xhr.open("GET", "/move?button=" + x, true);
     xhr.send();
   }
    function on(x) {
     var xhr = new XMLHttpRequest();
     xhr.open("GET", "/CAM?button=on", true);
     xhr.send();
   }
   function off(x) {
     var xhr = new XMLHttpRequest();
     xhr.open("GET", "/CAM?button=off", true);
     xhr.send();
   }
   
    setInterval(function ( ) {
  var xhttp = new XMLHttpRequest();
  xhttp.onreadystatechange = function() {
    if (this.readyState == 4 && this.status == 200) {
      document.getElementById("distance").innerHTML = this.responseText;
    }
  }
  xhttp.open("GET", "/distance", true);
  xhttp.send();
}, 500 ) 
setInterval(function ( ) {
  var xhttp = new XMLHttpRequest();
  xhttp.onreadystatechange = function() {
    if (this.readyState == 4 && this.status == 200) {
      document.getElementById("distance2").innerHTML = this.responseText;
    }
  }
  xhttp.open("GET", "/distance2", true);
  xhttp.send();
}, 500 ) 

setInterval(function ( ) {
  var xhttp = new XMLHttpRequest();
  xhttp.onreadystatechange = function() {
    if (this.readyState == 4 && this.status == 200) {
      document.getElementById("voltage").innerHTML = this.responseText;
    }
  }
  xhttp.open("GET", "/voltage", true);
  xhttp.send();
}, 1000 ) 

function updateSliderPWM(element) {
  var pwmSliderValue = document.getElementById("pwmSlider").value;
  document.getElementById("textSliderValue").innerHTML = pwmSliderValue;
  console.log(pwmSliderValue);
  var httpRequest = new XMLHttpRequest();
  httpRequest.open("GET", "/slider?value="+pwmSliderValue, true);
  httpRequest.send();
};
  </script>
</html>
)rawliteral";

//https://developer.mozilla.org/pl/docs/Web/API/XMLHttpRequest request
// wywolanie pierwszego wejscia do przegladarki
String processor(const String& var){
  //Serial.println(var);
  if(var == "DISTANCE"){
    return Front;
  }
  if(var == "DISTANCE2"){
    return Back;
  }
   if (var == "SLIDERVALUE"){
    return pwmSliderValue;
  }
  if (var == "VOLTAGE"){
    return v_measure();
  }
  if (var == "SLIDER"){
    return "10";
  }
  return String();
}
void Wifi_rozlaczono(WiFiEvent_t event, WiFiEventInfo_t info){
  Serial.print("Wifi utracone: ");
  Serial.println(info.disconnected.reason);
  Serial.println("...");
  move("stop");
  WiFi.begin(ssid, password);
  while (WiFi.status() != WL_CONNECTED) {
delay(500);
Serial.print(",");
}
}
void setup(){
   WRITE_PERI_REG(RTC_CNTL_BROWN_OUT_REG, 0); //disable   detector
Serial.begin(115200);// port szeregowy

mySerial.begin(115200, SERIAL_8N1, RXD2, TXD2);//115200 bit/s

pinMode(trigPin, OUTPUT); //
pinMode(echoPin, INPUT); //
pinMode(trigPin2, OUTPUT); //
pinMode(echoPin2, INPUT); //piny do obslugi HC-SR04

pinMode(v_baterry,INPUT);
pinMode(AIN2, OUTPUT);
pinMode(AIN1, OUTPUT);
digitalWrite(AIN1, LOW);
digitalWrite(AIN2, LOW);

pinMode(BIN2, OUTPUT);
pinMode(BIN1, OUTPUT);
digitalWrite(BIN1, LOW);
digitalWrite(BIN2, LOW);//piny obslugi sterownika silnikow


ledcSetup(1, 2000, 10);//inicjalizacja kanalu pwn
ledcSetup(9, 2000, 10);//inicjalizacja kanalu pwn
ledcAttachPin(PWMA,1);
ledcAttachPin(PWMB,9);
pinMode(PWMA,OUTPUT);
pinMode(PWMB,OUTPUT);//kanaly pwn
ledcWrite(1,0);//poczatkowa predkosc
ledcWrite(9,0);//poczatkowa predkosc

/*
  // polaczenie z wifi na stalym IP
  if (!WiFi.config(local_IP, gateway, subnet, primaryDNS, secondaryDNS)) {
Serial.println("STA Failed to configure");
}
*/
Serial.print("Łaczenie z  ");
Serial.println(ssid);
WiFi.begin(ssid, password);

while (WiFi.status() != WL_CONNECTED) {
delay(500);
Serial.print(",");
}

// wyswietlenie IP wybranego przez ruter
Serial.println("");
Serial.println("Wi-fi połaczone");
Serial.println("IP adres: ");
Serial.println(WiFi.localIP());
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
void loop() {
  if(left_encoder==true)
  {
  EncoderL();
  }
  
  if(abs(velocity)>90&&button!="stop")velocity = float(setpoint);
  if(abs(velocity)<5&button=="stop")velocity = 0;
  v1Prev = velocity;

  if(right_encoder==true)
  {
  EncoderP();
  }
  
  if(abs(velocity2)>90&&button!="stop")velocity2 = velocity;
  if(abs(velocity2)<5&button=="stop")velocity2 = 0;
  v1Prev = velocity;
  v2Prev = velocity2;

  if(button!="stop"&&interruptpi==true)
  {

  
  v1Filt= velocity;
  v1PrevF = velocity;
  
  
  e=float(setpoint)-v1Filt;
  deltaTC =0.001;
  calka=calka+e*deltaTC;
  u=kp*e+ki*calka;//+kd*dr;
  ep=e;
  if(u>920)u=920;
  if(u<=0)u=0;
  //u=240;
  ledcWrite(9, abs(u));

///////////////////////////////2 kolo
  v2Filt =velocity2;
  v2PrevF = velocity2;

   
   //e2=v1Filt-v2Filt;
   e2=float(setpoint)-v2Filt;
   calka2=calka2+e2*deltaTC;
   u2=kp2*e2+ki2*calka2;
  
  if(u2>920)u2=920;
  if(u2<=0)u2=0;
  
  /////ostatnie sterowanie
  
  e3=v1Filt-v2Filt;

   calka3=calka3+e3*deltaTC;
   u2=u2+kp3*e3+ki3*calka3;
   
  if(u2>920)u2=920;
  if(u2<=0)u2=0;
  
  //u2=240;
  ledcWrite(1, abs(u2));
  //////////////////////////////////////
  
  interruptpi=false;
  }

  if(interruptpomiar==true)
  {
    /*
  Serial.print(velocity);
  Serial.print(" ");
  Serial.print(velocity2);
  Serial.print(" ");
  Serial.print(setpoint);
  
  Serial.println();
  */
   
  interruptpomiar=false;
  }///do wykresow
  
   if(interruptdist==true)
  {
  Serial.println();
  Front_sensor();
  Back_sensor();
   
  interruptdist=false;
  }//do sensorow

  
}


  
  

void IRAM_ATTR check_EncoderL(){
  //a++;
  ///if(a==2)
  //{
  long currT = micros();
  deltaT = ((currT - prevT_i));
  prevT_i = currT;
  left_encoder=true;
  //a=0;
  //}
}

void  EncoderL(){
  // Read encoder B when ENCA rises
  /*
  if(button=="forward"||button=="right"){
    // If B is high, increment forward
    incrementL = 1;
  }
   if(button=="backward"||button=="left"){
    // Otherwise, increment backward
    incrementL = -1;
  }
  */
  //pos_i = pos_i + increment;
  //long currT = micros();
  //long deltaT = ((currT - prevT_i));
  velocity = ((1000000.0)/(float(deltaT)))/(960.0/60.0);//idealny sposob
  //velocity = ((increment*1000000.0)/(float(deltaT)))/(192.0/60.0);//idealny sposob
  //prevT_i = currT;

  
  left_encoder=false;
}
void IRAM_ATTR check_EncoderP(){
  //a++;
  ///if(a==2)
  //{
  long currT = micros();
  deltaTP = ((currT - prevT_iP));
  prevT_iP = currT;
  right_encoder=true;
  //a=0;
  //}
}

void  EncoderP(){
  // Read encoder B when ENCA rises
  /*
  if(button=="forward"||button=="left"){
    // If B is high, increment forward
    incrementP = 1;
  }
   if(button=="backward"||button=="right"){
    // Otherwise, increment backward
    incrementP = -1;
  }
  */
  velocity2 = ((1000000.0)/(float(deltaTP)))/(960.0/60.0);//idealny sposob
 
  
  right_encoder=false;
}

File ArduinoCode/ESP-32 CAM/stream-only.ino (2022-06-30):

#include <WiFi.h>
#include "esp_timer.h"
#include "img_converters.h"
#include "Arduino.h"
#include "fb_gfx.h"
#include "soc/soc.h"             // wyłącza wykrycie brownoutu
#include "soc/rtc_cntl_reg.h"    // wyłącza wykrycie brownoutu - typowe przy tym modelu
#include "esp_http_server.h"
#include "esp_camera.h"

const char *ssid = "Orange_Swiatlowod_095A";  //nazwa wi-fi
const char *password = "WWZYKLF6PR4V";        //hasło wi-fi

/*
// IP statyczne
IPAddress local_IP(192,168,1,28);
//http://192.168.1.27/stream 
IPAddress gateway(192,168,1,1);

IPAddress subnet(255, 255, 255, 0);
IPAddress primaryDNS(8, 8, 8, 8);
IPAddress secondaryDNS(8, 8, 4, 4);
*/


String komenda = "";//zmienna do kumunikacji UART

void setup() {
  WRITE_PERI_REG(RTC_CNTL_BROWN_OUT_REG, 0); //wyłaczenie brownoutu
  Serial.begin(115200);//ustawienie szybkosci transmisji portu szeregowego w bit/s
  
  camera_ini();//obsługa kamery w drugim pliku
/*
  // Wi-Fi connection
if (!WiFi.config(local_IP, gateway, subnet, primaryDNS, secondaryDNS)) {
Serial.println("STA Failed to configure");
}//przypadek uzycia własnorecznie wybranego IP
*/
Serial.print("Łaczenie z  ");
Serial.println(ssid);
WiFi.begin(ssid, password);

while (WiFi.status() != WL_CONNECTED) {
delay(500);
Serial.print(",");
}

// wyswietlenie IP wybranego przez ruter
Serial.println("");
Serial.println("Wi-fi połaczone");
Serial.println("IP adres: ");
Serial.println(WiFi.localIP());

startCameraServer();

pinMode(4, OUTPUT);

digitalWrite(4, HIGH);
delay(500);
digitalWrite(4, LOW);
//zaświecenie dioda LED
//sygnalizacji udanej inicjalizacji programu
}

void loop() {

   if(Serial.available() > 0) {
    //jezeli port dostepny
    komenda = Serial.readStringUntil('\n');
    // zapis otrzymane polecenie w zmiennej
    
     //obsługa LEDU
     if (komenda.startsWith("on"))  
     digitalWrite(4, HIGH);
     if (komenda.startsWith("off"))  
     digitalWrite(4, LOW);

     //ustawienie efektu
     if (komenda.startsWith("Gray"))  
     {
     sensor_t * s = esp_camera_sensor_get();
     s->set_special_effect(s, 2);
     }
     if (komenda.startsWith("No Effect"))  
     {
     sensor_t * s = esp_camera_sensor_get();
     s->set_special_effect(s, 0);
     }
     
     //zmiana rozdzielczości
     if (komenda.startsWith("VGA"))  
     {
      sensor_t * s = esp_camera_sensor_get();
      s->set_framesize(s, FRAMESIZE_VGA);
     }
     if (komenda.startsWith("HVGA"))  
     {
      sensor_t * s = esp_camera_sensor_get();
      s->set_framesize(s, FRAMESIZE_HVGA);
     }

     //Zmiana jakości
     if (komenda.startsWith("quality")) 
     {
      sensor_t * s = esp_camera_sensor_get();
      komenda.replace("quality","");
      int set=komenda.toInt();
      s->set_quality(s, set);
     }
     
   }
   
   
}
